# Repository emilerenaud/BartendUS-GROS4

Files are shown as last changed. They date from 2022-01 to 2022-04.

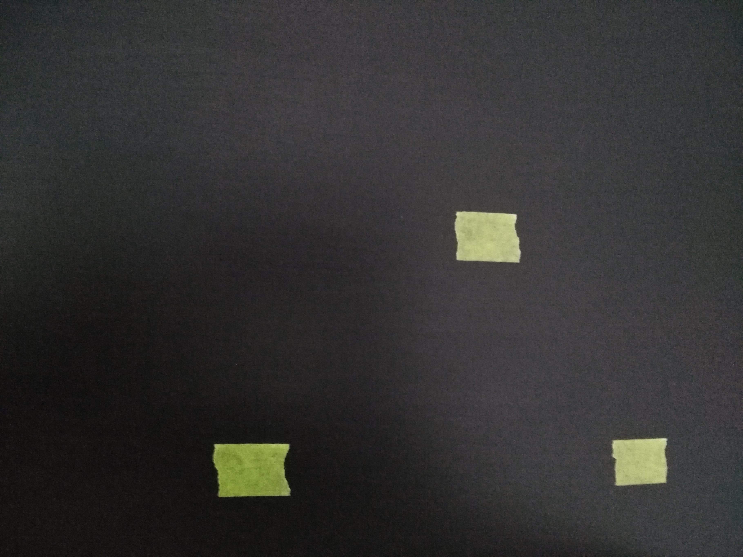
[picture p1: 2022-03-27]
Logiciel/Vision/img_to_seuil.png

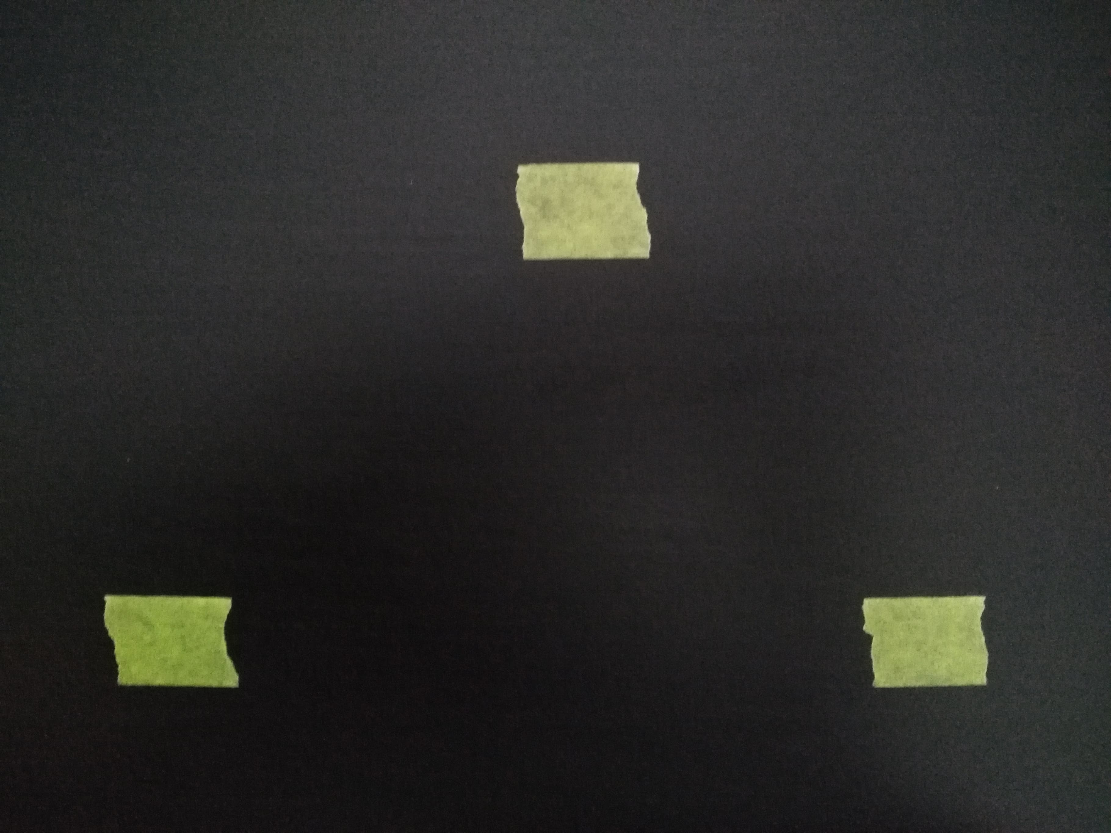
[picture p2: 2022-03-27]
Logiciel/Vision/img_reference_calib_V2.png

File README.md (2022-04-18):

# BartendUS 
## GRO-S4H2022 - Université de Sherbrooke

BartendUS est un projet académique de 4e session du programme de génie robotique de l'Université de Sherbrooke réalisé par 6 étudiants. C'est un projet réalisé dans le cadre du cours _GRO400:_ _Conception agile et ouverte en robotique_.

BartendUS est une plateforme surmontée d'un bras robotisé de type SCARA qui permet de créer des breuvages alcoolisés sur mesure. Le robot est assisté par un algorithme de vision ainsi qu'une interface utilisateur graphique. Également, des supports conçus sur mesure permettent le maintien des bouteilles en place tout en facilitant la distribution des liquides.



## Table des matières
* Présentation de l'équipe
* Vidéo promotionnelle du projet
* Requis matériel
* Installation
* Licence

## Présentation de l'équipe


*De gauche à droite: Simon Chayer, Émile Renaud, Antoine Landry, Hugues Dupuis et Thomas Landry*

IMPORTANT : Sur cette photo, il manque un membre de l'équipe : Frédéric Forest, qui ne pouvait pas être présent lors de la présentation.

## Vidéo promotionnelle du projet
Voici une vidéo réalisée par Antoine Landry mettant en vedette la solution développée tout au long de la session:
https://www.youtube.com/watch?v=95p3Jdjmmvk

## Requis matériel
- Un bras robotisé SCARA et sa plateforme. Les instructions d'assemblage sont disponibles dans [le répertoire « Mécanique »](https://github.com/mimil2014/BartendUS-GROS4/tree/main/M%C3%A9canique).
- Distributeur d'alcool et le support sur mesure. Les plans sont disponibles dans [le répertoire « Mécanique »](https://github.com/mimil2014/BartendUS-GROS4/tree/main/M%C3%A9canique).
- Éléments présentés dans le [BOM](https://github.com/mimil2014/BartendUS-GROS4/blob/main/BOM/liste_pieces.pdf).

## Installation 
### Installation des librairies sur le RaspberryPi:
Assurez-vous que votre Pi est à jour avec les commandes suivantes: 
```
sudo apt update  
sudo apt upgrade  
```
Installer le terminal Terminator (si vous désirez):   
```
sudo apt-get install terminator   
```
Installer Python sur le Pi:   
```
sudo apt install python3-dev   
sudo apt-get install python3-pip 
```
À partir du fichier requirements.txt, installer les librairies avec la commande: 
```
pip3 install -r requirements.txt  
```
Cette commande installera toutes les librairies nécessaires au projet sur votre Pi. Si vous avez de la difficulté à installer OpenCV, vous pouvez suivre les étapes du site suivant:   https://singleboardbytes.com/647/install-opencv-raspberry-pi-4.htm

*Prendre note que la version installée pour ce projet est la version courte détaillée sur le site.

De la façon suggérée sur ce site, les librairies sont installées dans un environnement virtuel. Il faut seulement s'assurer que les autres librairies utilisées     dans le projet sont également dans cet environnement virtuel. 

## Licence
BSD License

Voir [LICENSE](LICENSE)

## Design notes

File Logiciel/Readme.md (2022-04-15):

# Explication des différents sous-dossiers:

## Vision: 
- Calibration de la caméra 
- Détection du seuil

## *pi_controller*:
- Gestion de l'HMI ("*front-end*" et "*back-end*")
- Cinématique inverse
- *Main* du robot
- *State machine*
- Gestion des recettes 
- Gestion des ingéridents et quantités
- Algorithme de détection centre des verres

## *scara_controller*:
- Gestion des moteurs
- Gestion des pompes
- Algorithme de versement
- Algorithme de "*homing*"

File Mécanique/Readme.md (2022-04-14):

# Guide de montage mécanique du robot

Voir le document pdf suivant : [Guide d'assemblage](https://github.com/mimil2014/BartendUS-GROS4/blob/main/M%C3%A9canique/Guide%20d'assemblage%20du%20robot.pdf)

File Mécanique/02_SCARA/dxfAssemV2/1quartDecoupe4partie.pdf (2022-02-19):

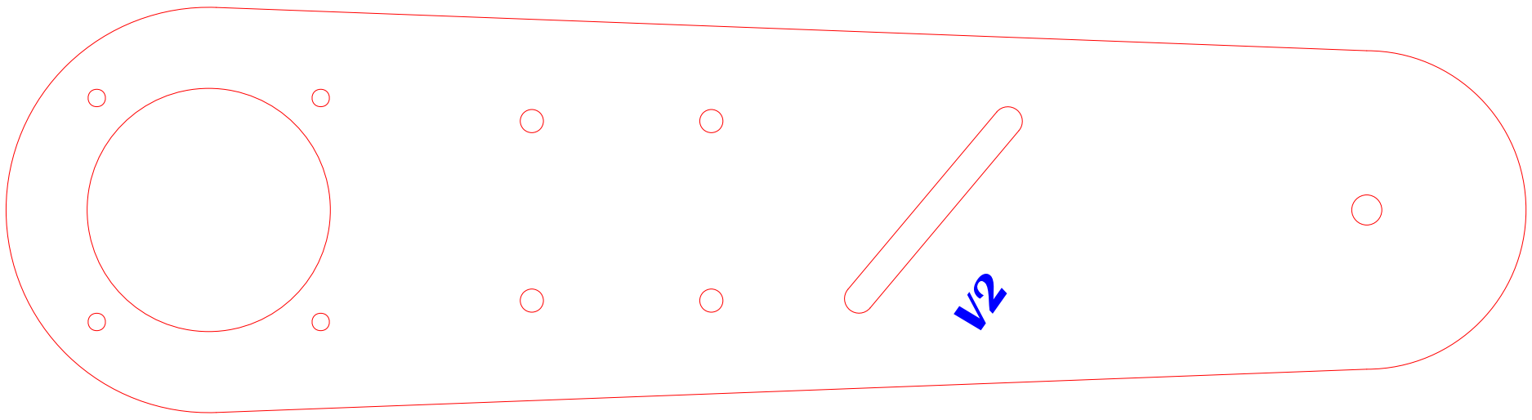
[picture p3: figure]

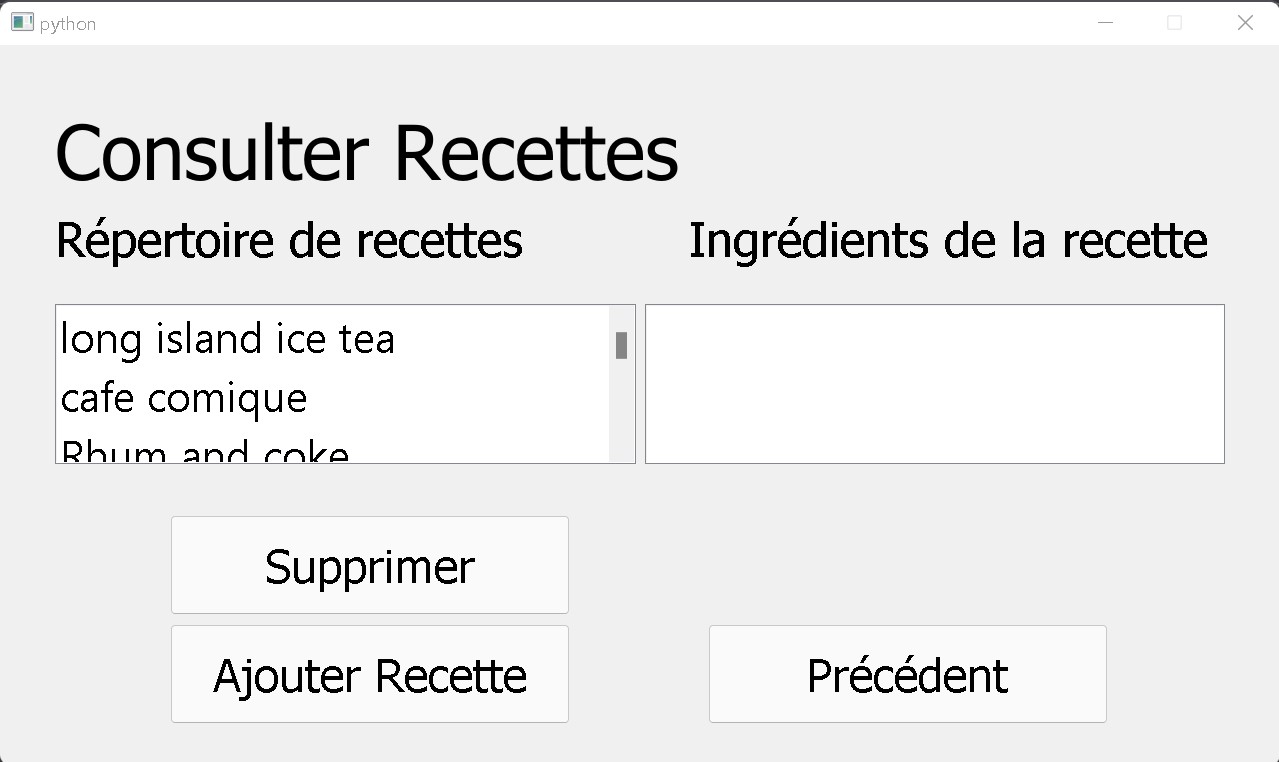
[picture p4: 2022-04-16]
Images/HMI/ecran_consulter_recettes.jpg

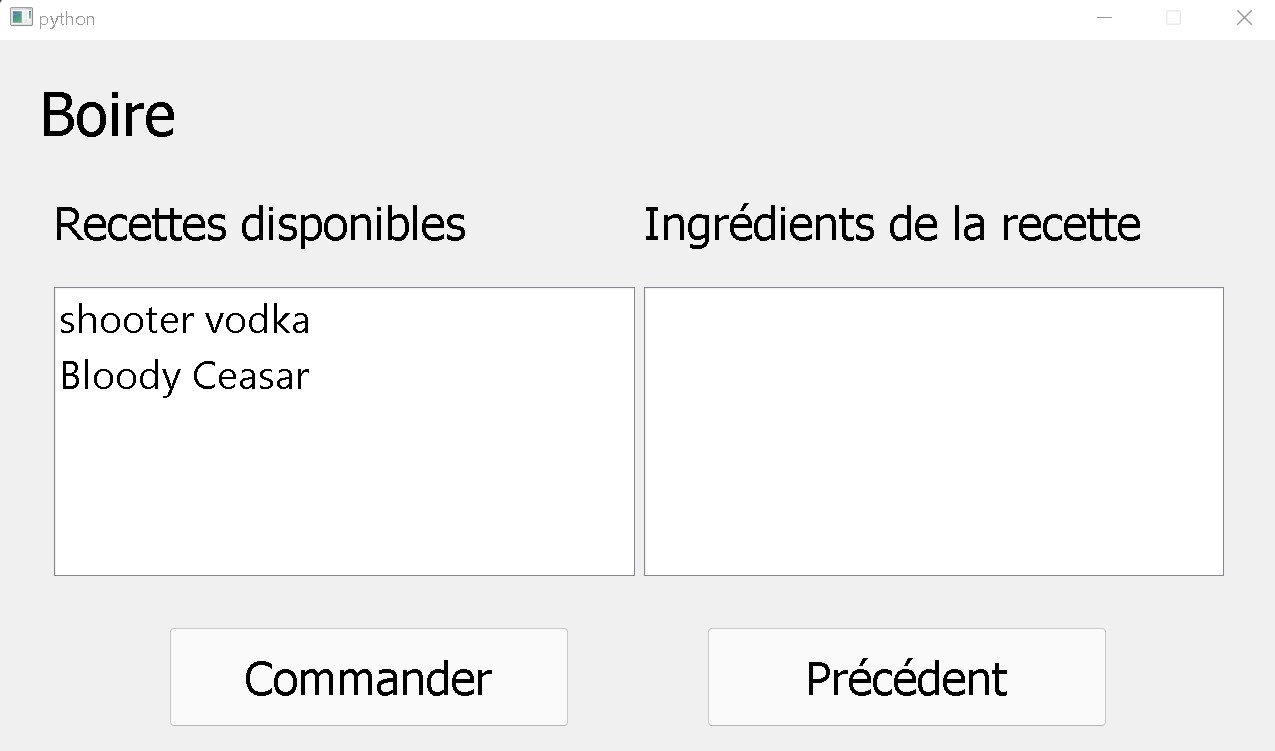
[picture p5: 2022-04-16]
Images/HMI/ecran_boire.jpg

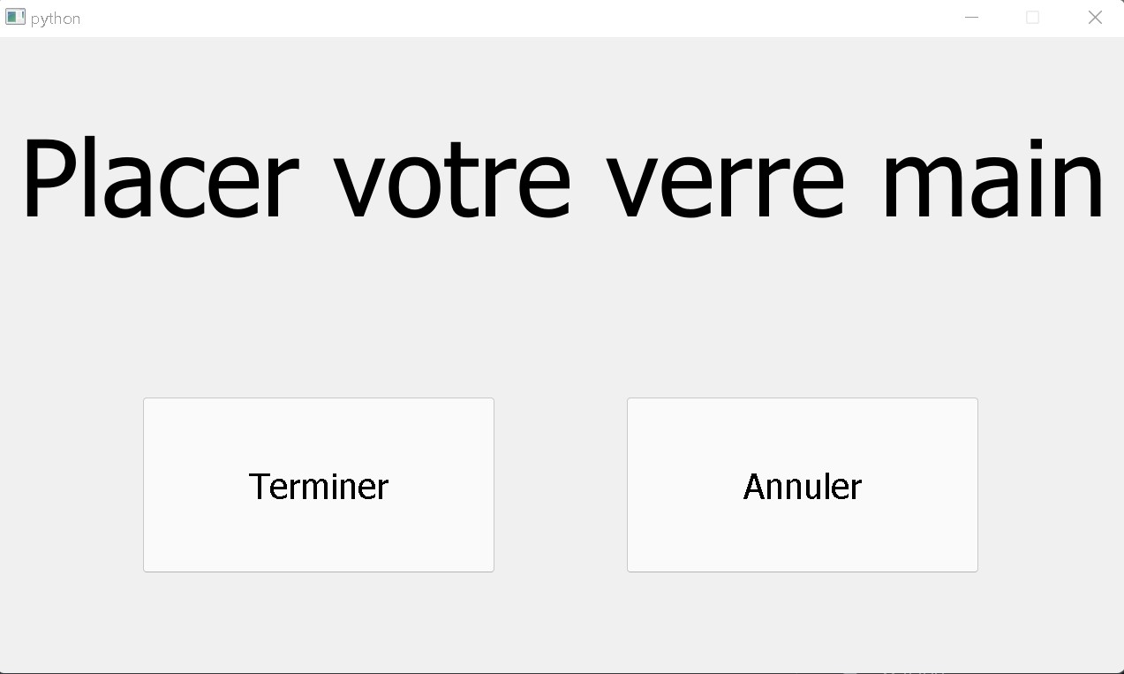
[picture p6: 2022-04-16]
Images/HMI/ecran_commander.jpg

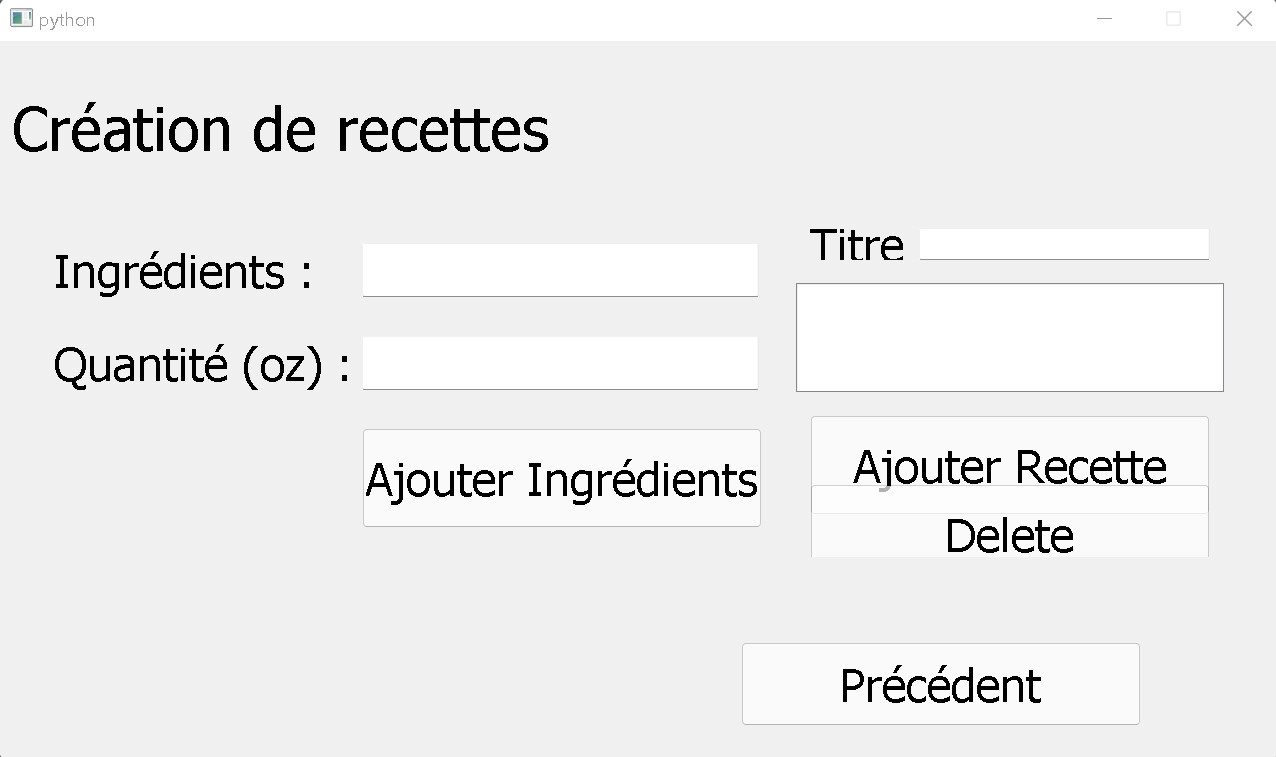
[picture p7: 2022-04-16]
Images/HMI/ecran_ajouter_recette.jpg

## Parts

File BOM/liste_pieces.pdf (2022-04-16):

Domaine | Pièces | Partie du
Robot | Description
Quantité | Coût unitaire | Lieu d’achat | Coût total (CAD)
| (CAD)

Mécanique

Coupleur Nema 17 | Base | | 2 | 2,60 | Amazon | 5,20
Moteur Nema 17 (33
mm) | Base | 33 mm | 3 | 30,03 | Amazon | 90,09
Lead screw | Base | 310 mm T8x8 | 1 | 13,18 | Amazon | 13,18
Tige en acier
inoxydable | Base | 8 x 300 mm | 3 | 21,00 | Amazon | 63,00
Lead Screw Nut | Base | T8 | 2 | 5,00 | Amazon | 10,00
Roulement à billes
pour planche à roulettes | Base | 8 x 22 x 7 mm | 1 | 2,98 | Amazon | 2,98
M4 10 mm + écrou | Base | - | 6 | 0,15 | Amazon | 0,90
M5 10 mm + écrou | Base | - | 13 | 0,15 | Amazon | 1,95
M5 16 mm + écrou | Base | - | 22 | 0,15 | Amazon | 3,30
M5 60 mm + écrou | Base | - | 6 | 0,15 | Amazon | 0,90
Linear Ball Bearings | Chariot | D. axe : 8 mm | 6 | 8,00 | Amazon | 48,00
M3 16 mm + écou | Chariot | - | 4 | 0,15 | Amazon | 0,60
M3 16 mm tête
fraisée + écrou | Chariot | - | 11 | 0,15 | Amazon | 1,65
M3 20 mm + écrou | Chariot | - | 27 | 0,15 | Amazon | 4,05
M5 50 mm + écrou | Chariot | - | 1 | 0,15 | Amazon | 0,15
M8 40 mm + écrou | Chariot | - | 1 | 0,15 | Amazon | 0,15
Thrust ball bearing | Bras | 20 x 40 x 14 mm | 4 | 10,00 | Amazon | 40,00
Micro Servo Moteur
pour RC | Bras | SG90 9 g | 1 | 6,99 | Amazon | 6,99

M3 8 mm tête fraisée
+ écrou | Bras | - | 12 | 0,15 | Amazon | 1,80
M3 10 mm + écrou | Bras | - | 8 | 0,15 | Amazon | 1,20
M4 30 mm + écrou | Bras | - | 4 | 0,15 | Amazon | 0,60

Tableau 1 : Liste de pièces exhaustive du projet

M5 50 mm + écrou Bras

2 | 0,15 | Amazon | 0,30
Shaker | Bras

1 | 35,00 | Amazon | 35,00
M3 10 mm + écrou | Caméra

3 | 0,15 | Amazon | 0,45
M3 16 mm + écrou | Caméra

1 | 0,15 | Amazon | 0,15
M4 16 mm + écrou | Caméra

4 | 0,15 | Amazon | 0,60
Tuyau en aluminium
pour caméra | Caméra | 3,5 pi
1 | 20,00 | Amazon | 20,00
M5 35 mm+ écrou | Distributeur

4 | 0,15 | Amazon | 0,60
Pompe à Membrane 6-12V | Distributeur | R385 DC
6 | 13,9
| 8 | Amazon | 83,88

Tube en silicone

flexible | Distributeur | 6 x 8 mm, Longueur
: 5 m
| | 1 | 16,99 | Amazon | 16,99

Moteur Nema 17 (48
mm) | Chariot/Bras | 48 mm
| | 2 | 13,99 | Amazon | 27,98

Bore Timing Pulley
Idler With Bearing | Chariot/Bras | GT2 20T 5mm Bore
| | 2 | 4,00 | Amazon | 8,00

Bore Timing Belt Idler
Pulley Flange With
Bearing
Chariot/Bras | GT2 20T 5mm Bore | 2 | 3,99 | Amazon | 7,98
Open Belt | Chariot/Bras | GT2 LL
| -2GT -6 (6 mm
| wide)
- 1890 mm
| | 1 | 15,00 | Amazon | 15,00

Inserts M3 pour
impression 3D

Chariot/Bras/
Base | Hauteur : 7mm | 20 | 0,25 | Amazon | 5,00

Passe fil

- | - | 1 | 5,00 | Amazon | 5,00
Contre

-plaqué
merisier russe
- 5 pi x 5 pi
| | 1 | 50,00 | Rona | 50,00

Électrique

Raspberry Pi 4 Starter
Kit
- 4GB RAM
1 | 149,95 | Amazon | 149,95

Arduino Mega 2560
Rev3

1 | 50,64 | Amazon | 50,64

CNC shield

Carte d'extension
Longruner GRBL
CNC Shield V3.0 +
pilote moteur pas à
pas A4988 avec
dissipateur
thermique
1 | 30,99 | Amazon | 30,99

Transistor

- 2N2222
6 | 0,50 | Amazon | 3,00
Diode
- 1N4007

T

6 | 0,30 | Amazon | 1,80

Power Supply

Entrée universelle :
100

-240 V CA ;
sortie : 12 V CC 5 A
1 | 20,99 | Amazon | 20,99
Fiches d'aviation | Distributeur

4 broches 16 mm
GX16

-4 en métal
mâle

-femelle

4 | 3,86 | Amazon | 15,45

Écran tactile
- 7 " de diagonale
1 | 120,00 | Amazon | 120,00
Limit switch | Chariot/Bras/
Base

3 | 0,35 | Amazon | 1,05

Caméra

Caméra

1 | 10,00 | Amazon | 10,00
Électro
-aimant | Bras

1 | 20,00 | Amazon | 20,00
Câble USB

1 | 4,00 | Amazon | 4,00
Total | 1001,49

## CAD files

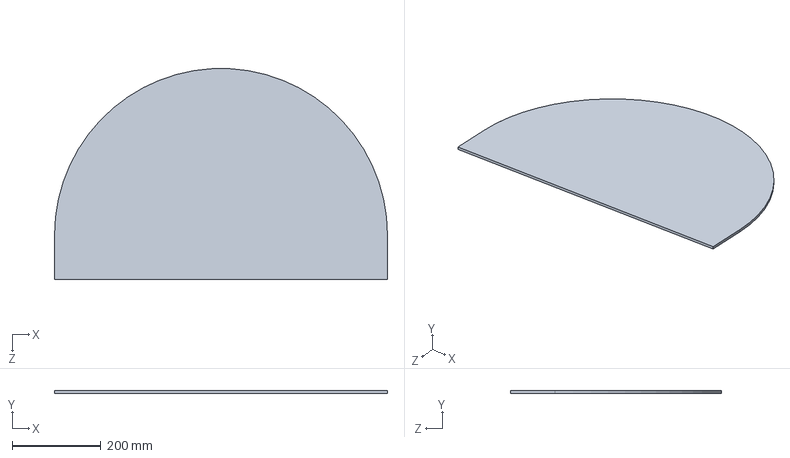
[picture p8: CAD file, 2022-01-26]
Mécanique/00_Assy_BartendUS.SLDASM
750.0 x 6.35 x 474.5 mm

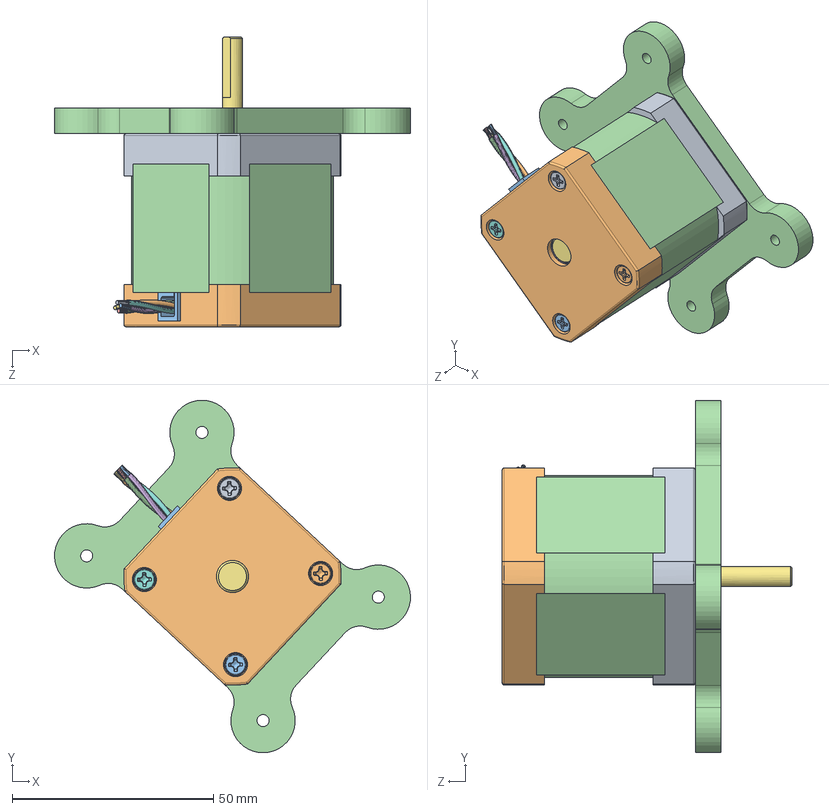
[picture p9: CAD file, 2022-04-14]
Mécanique/02_SCARA/V3/chariotTEST/assemblage_support_stepper_v2_temp.SLDASM
88.5 x 87.6 x 72.0 mm
Frontplate.step
Backplate.step
Connenctor.step
Housing.step
Bearing dummy.step
Bearing dummy 01.step
Core.step
M3x40-Screw.step
M3x40-Screw001.step
M3x40-Screw002.step
M3x40-Screw003.step
Cable-1of4.step
Copper-1of4.step
Cable-2of4.step
Copper-4of4.step
Cable-3of4.step
Copper-3of4.step
Cable-4of4.step
Copper-2of4.step
supportMoteurTop

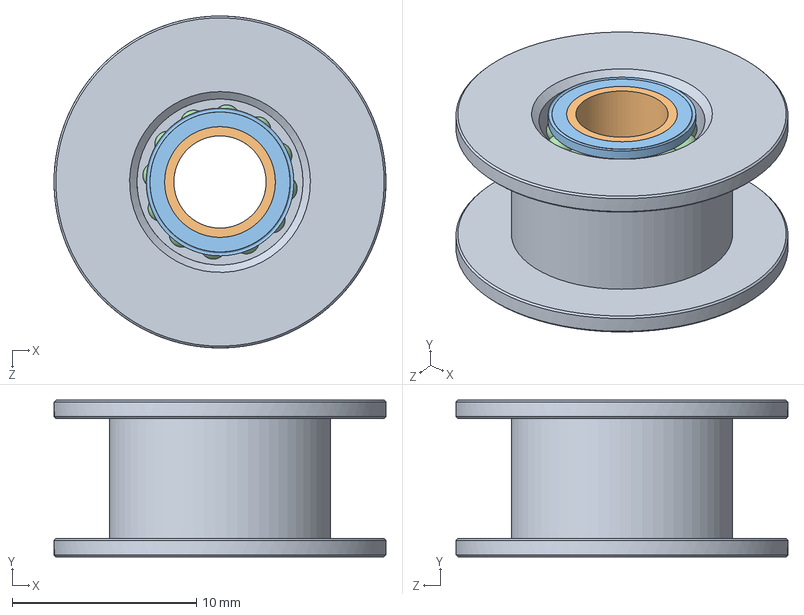
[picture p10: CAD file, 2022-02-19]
Mécanique/99_Library/gt2-pulley-16-20-without-teeth-bore-3-4-5-mm-for-gt2-belt-width-6-10-mm-1.snapshot.84/GT2 Idler Pulley, Configurable.SLDASM
18.0 x 8.50 x 18.0 mm
Body, GT2 Idler Pulley, Configurable
Bearing Inner Ring, GT2 Idler Pulley, Configurable x 2
Bearing Seal, GT2 Idler Pulley, Configurable x 4
Bearing Ball, GT2 Idler Pulley, Configurable x 24

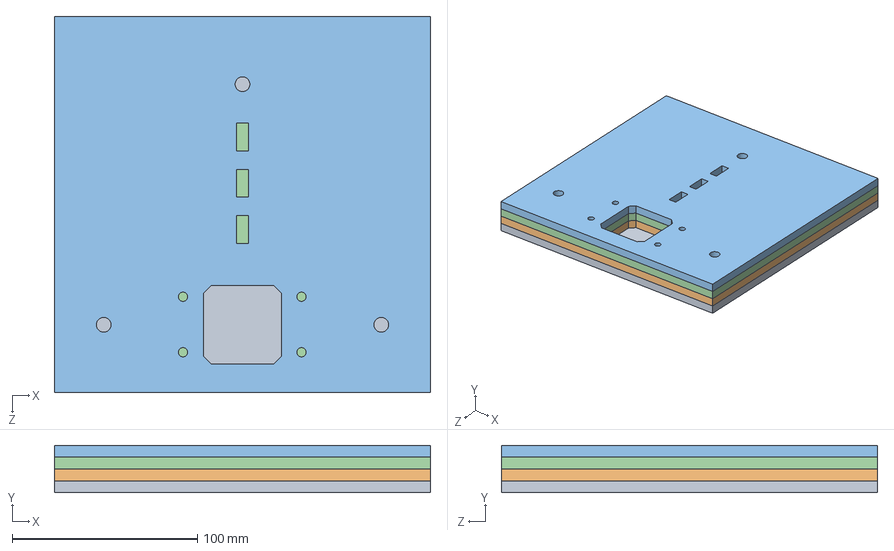
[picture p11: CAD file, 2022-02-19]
Mécanique/02_SCARA/V3/Z-axis/02_01_Assy_base_z_axis_V1.SLDASM
203.2 x 25.4 x 203.2 mm
02_03_plaque_fond_base
02_05_deuxieme_niveau_base
02_06_troixieme_niveau_base
02_012_deuxieme_v2_niveau_base

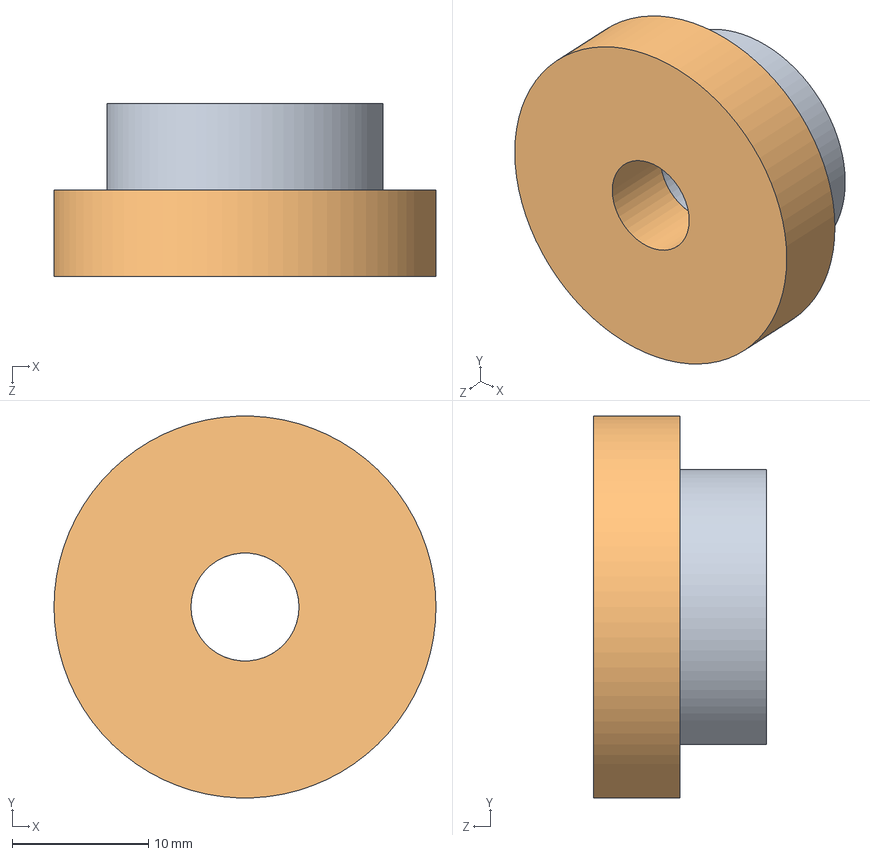
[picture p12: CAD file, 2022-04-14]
Mécanique/03_Supp_distri/V3/assemblage_bouchon.SLDASM
28.0 x 28.0 x 12.7 mm
partie_inf_bouchon_bouteille
partie_supp_bouchon_bouteille

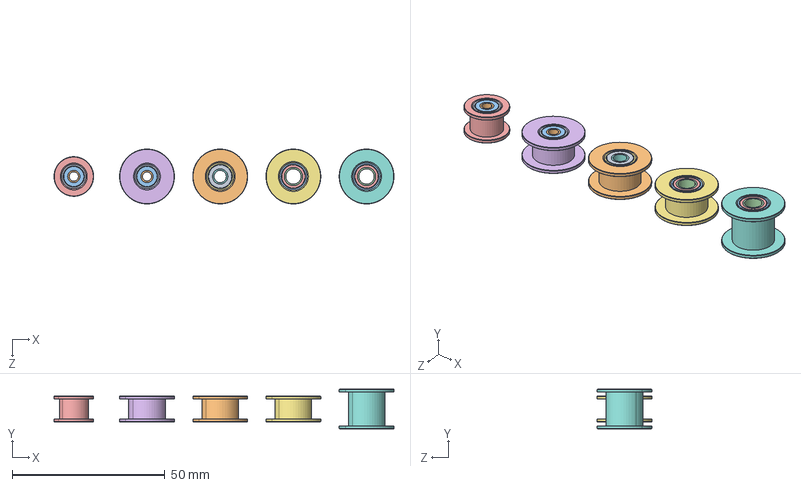
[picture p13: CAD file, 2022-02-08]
Mécanique/99_Library/gt2-pulley-16-20-without-teeth-bore-3-4-5-mm-for-gt2-belt-width-6-10-mm-1.snapshot.84/GT2 Idler Pulley, Configurable, Pulleys Lined Up in Assembly.STEP.SLDASM
111.5 x 13.0 x 18.0 mm
Bearing Outer Ring, GT2 Idler Pulley, Configurable_3 mm Bore.STEP x 4
Bearing Inner Ring, GT2 Idler Pulley, Configurable_3 mm Bore.STEP x 4
Bearing Seal, GT2 Idler Pulley, Configurable_3 mm Bore.STEP x 8
Bearing Ball, GT2 Idler Pulley, Configurable_2 mm.STEP x 40
Body, GT2 Idler Pulley, Configurable_16T W6 B3 Without T.STEP
Body, GT2 Idler Pulley, Configurable_20T W6 B3 Without T.STEP
Bearing Outer Ring, GT2 Idler Pulley, Configurable_4 mm Bore.STEP x 2
Bearing Inner Ring, GT2 Idler Pulley, Configurable_4 mm Bore.STEP x 2
Bearing Seal, GT2 Idler Pulley, Configurable_4 mm Bore.STEP x 4
Body, GT2 Idler Pulley, Configurable_20T W6 B4 Without T.STEP
Bearing Outer Ring, GT2 Idler Pulley, Configurable_5 mm Bore.STEP x 4
Bearing Inner Ring, GT2 Idler Pulley, Configurable_5 mm Bore.STEP x 4
Bearing Seal, GT2 Idler Pulley, Configurable_5 mm Bore.STEP x 8
Bearing Ball, GT2 Idler Pulley, Configurable_1.4 mm.STEP x 48
Body, GT2 Idler Pulley, Configurable_20T W6 B5 Without T.STEP
Body, GT2 Idler Pulley, Configurable_20T W10 B5 Without T.STEP

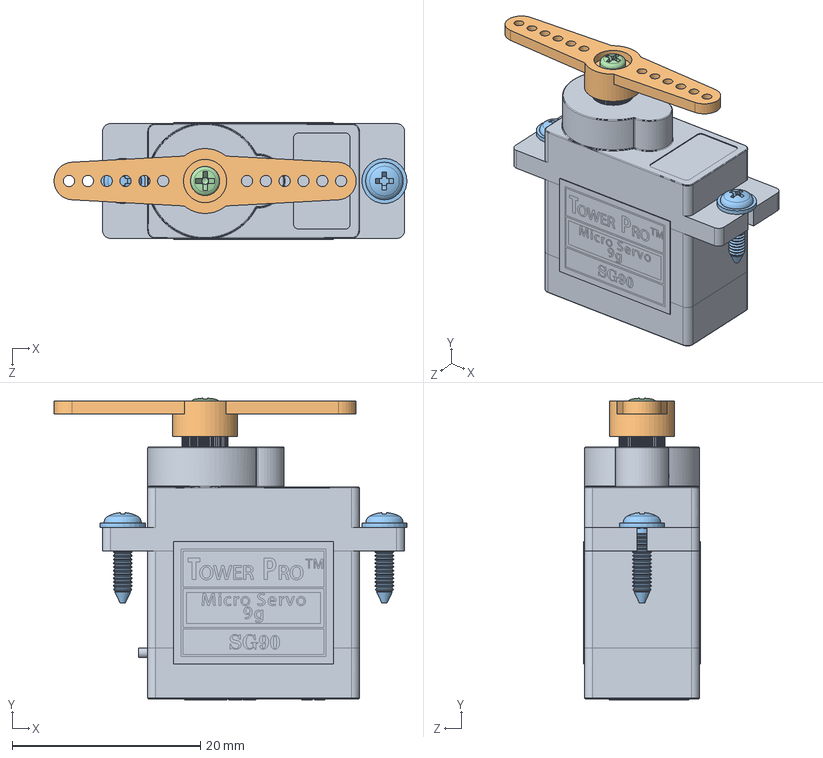
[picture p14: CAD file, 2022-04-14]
Mécanique/99_Library/SG90 - Micro Servo 9g - Tower Pro.SLDASM
37.5 x 32.0 x 12.4 mm
SG90 - Micro Servo 9g - Tower Pro.1
SG90 - Micro Servo 9g - Tower Pro.3
SG90 - Micro Servo 9g - Tower Pro.5 x 2
SG90 - Micro Servo 9g - Tower Pro.6

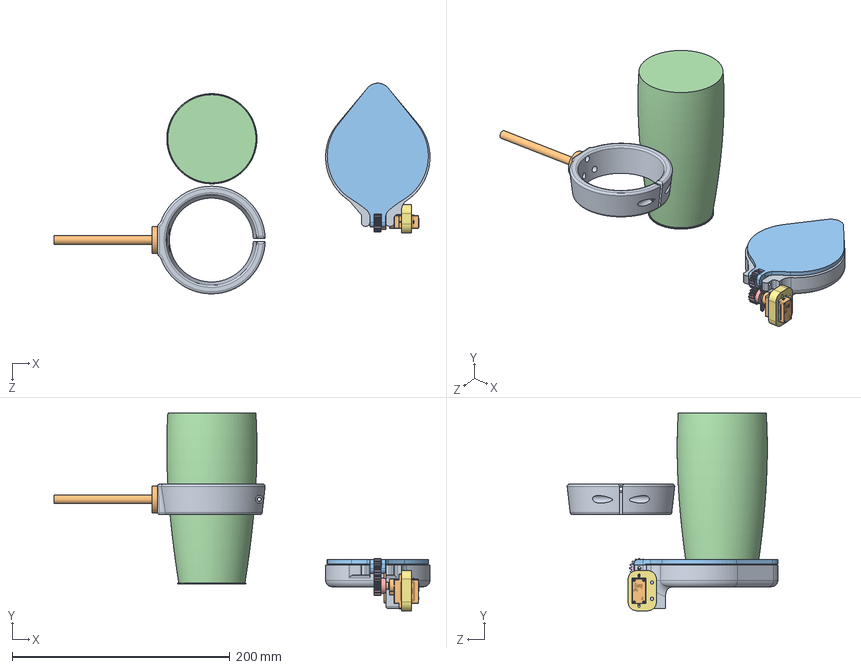
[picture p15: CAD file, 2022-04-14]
Mécanique/Shaker/Assem2.SLDASM
345.7 x 181.7 x 193.8 mm
topShaker
SG90 - Micro Servo 9g - Tower Pro
coverV2
shaker
ServoGear
coverGear
suuportServo
gasketproto2
supportShakerV3
shaft

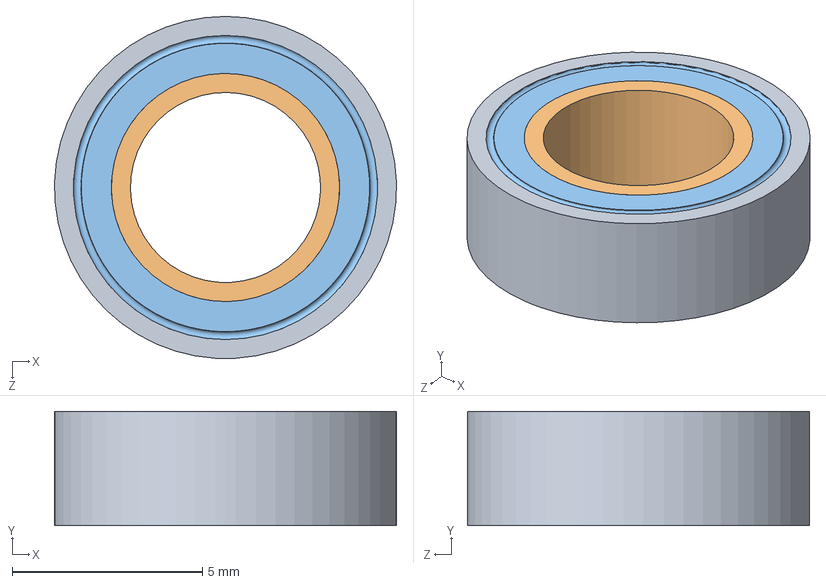
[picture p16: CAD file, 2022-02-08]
Mécanique/99_Library/gt2-pulley-16-20-without-teeth-bore-3-4-5-mm-for-gt2-belt-width-6-10-mm-1.snapshot.84/Bearing Subassy, GT2 Idler Pulley, Configurable.SLDASM
9.00 x 3.00 x 9.00 mm
Bearing Outer Ring, GT2 Idler Pulley, Configurable
Bearing Inner Ring, GT2 Idler Pulley, Configurable
Bearing Seal, GT2 Idler Pulley, Configurable x 2
Bearing Ball, GT2 Idler Pulley, Configurable x 12

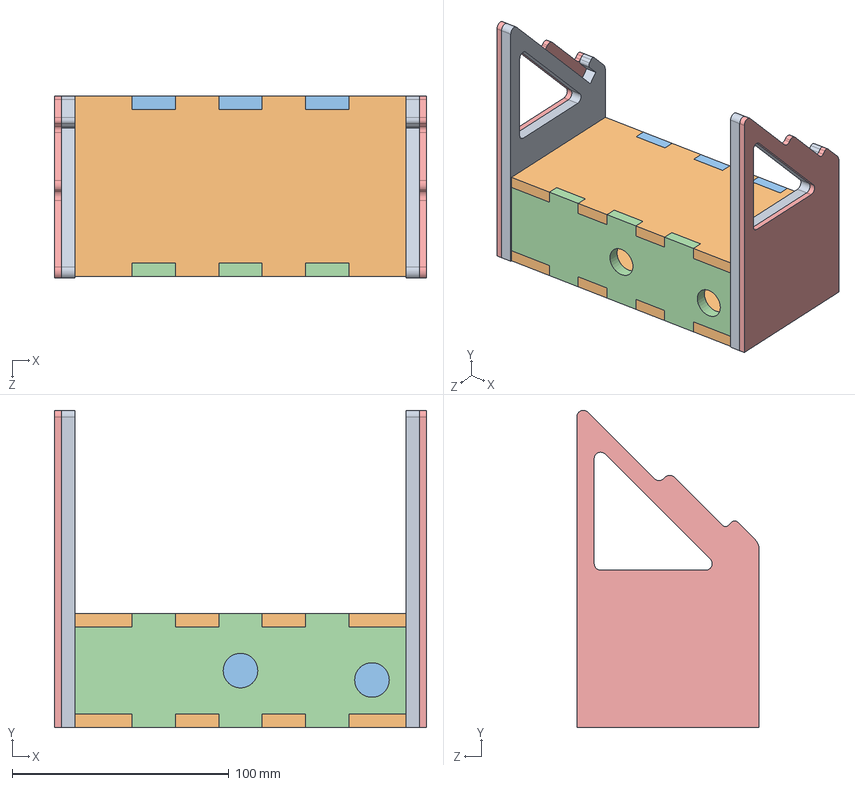
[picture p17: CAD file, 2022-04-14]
Mécanique/01_Base/V1/Support écran/ass_support_ecran.SLDASM
171.7 x 146.5 x 84.1 mm
montant_exterieur_support_ecran x 2
plancher_support_ecran x 2
face_support_ecran
arriere_support_ecran
montant_exterieur_support_ecran_1_8 x 2

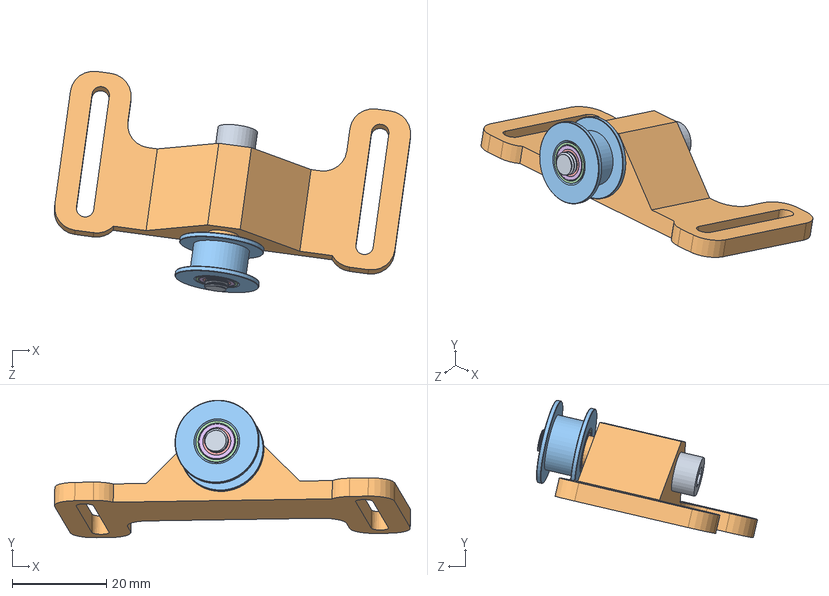
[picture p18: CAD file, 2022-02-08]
Mécanique/99_Library/gt2-pulley-16-20-without-teeth-bore-3-4-5-mm-for-gt2-belt-width-6-10-mm-1.snapshot.84/AssemSupportPoulie.SLDASM
75.7 x 29.3 x 47.1 mm
M5x30.stp
supportPoulieV2
Body, GT2 Idler Pulley, Configurable
Bearing Outer Ring, GT2 Idler Pulley, Configurable x 2
Bearing Inner Ring, GT2 Idler Pulley, Configurable x 2
Bearing Seal, GT2 Idler Pulley, Configurable x 4
Bearing Ball, GT2 Idler Pulley, Configurable x 24

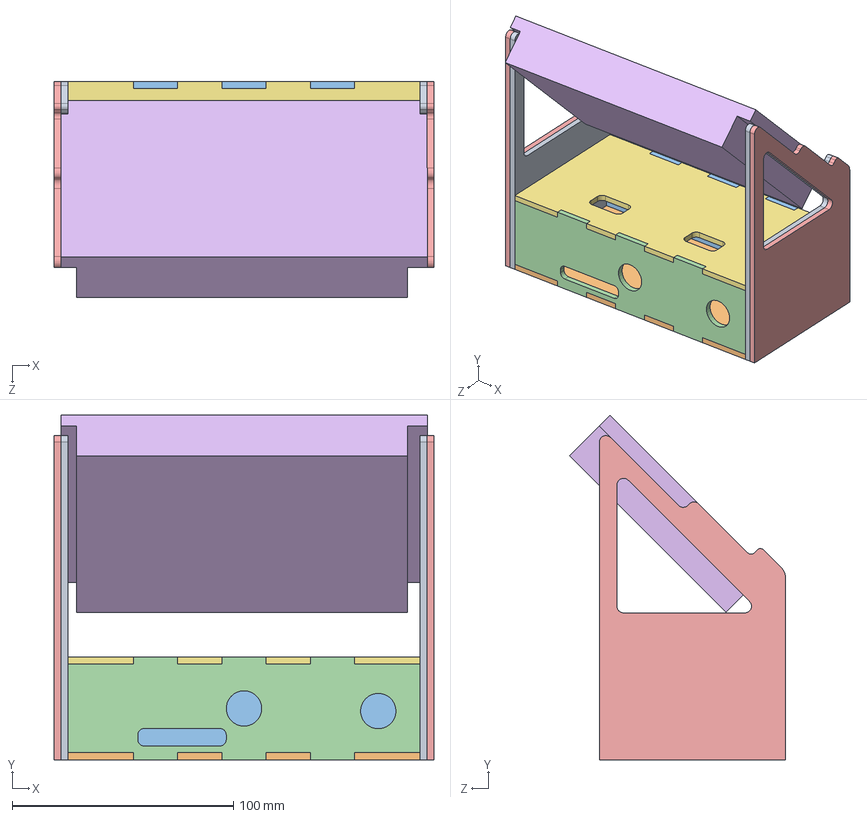
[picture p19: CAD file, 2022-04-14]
Mécanique/01_Base/V1/Support écran/1_8_po/support_ecran_1_8_po.SLDASM
171.7 x 155.7 x 97.6 mm
montant_exterieur_support_ecran_1_8_int x 2
plancher_support_ecran_1_8
face_support_ecran_1_8
arriere_support_ecran_1_8
montant_exterieur_support_ecran_1_8 x 2
ecran_7po
plancher_support_ecran_1_8_trous

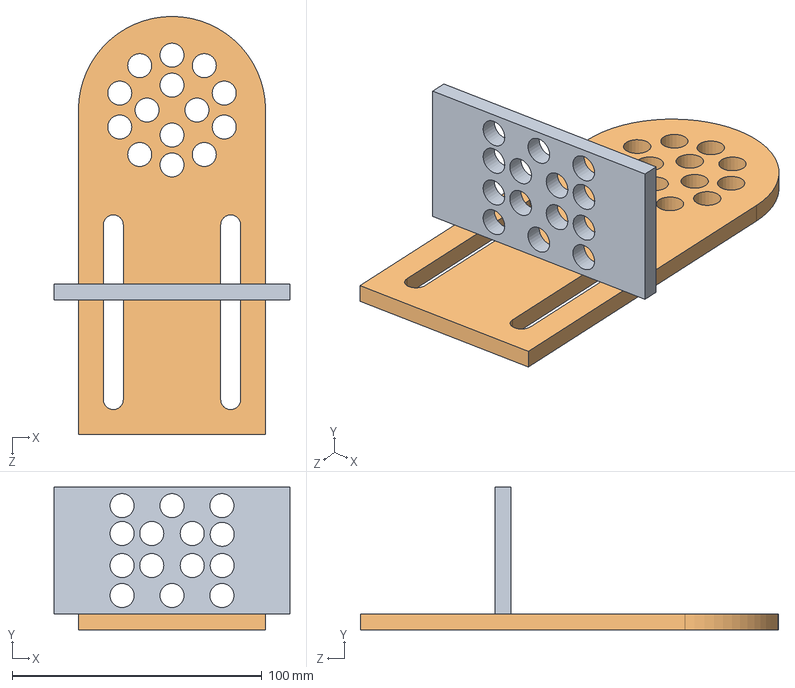
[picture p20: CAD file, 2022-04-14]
Mécanique/03_Supp_distri/V3/Assem.SLDASM
94.5 x 57.2 x 167.5 mm
protoDistributeurTOP
protoDistributeur

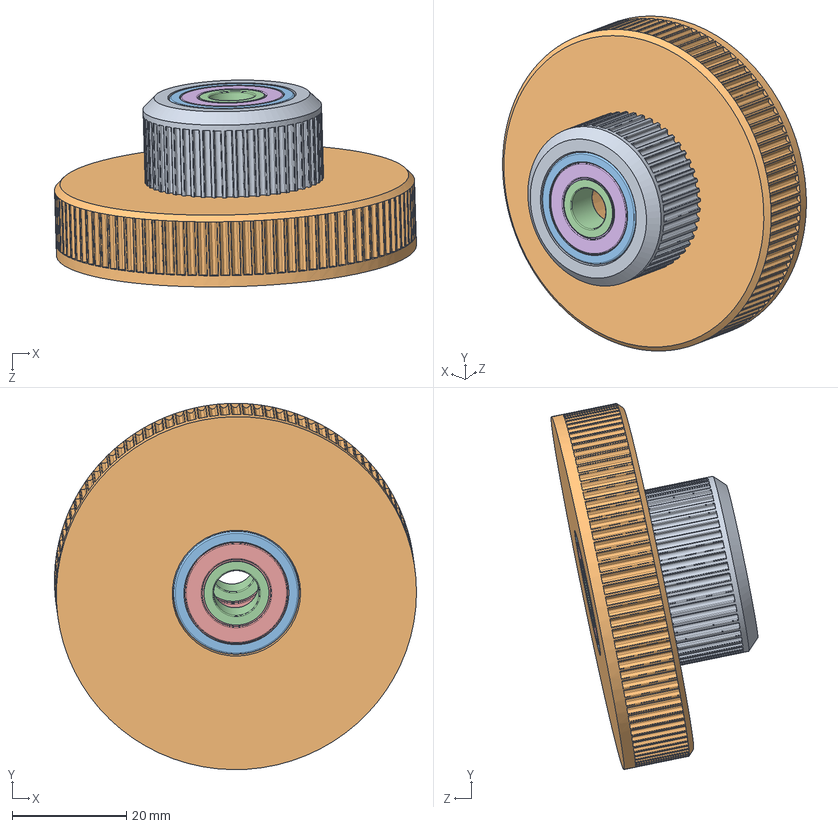
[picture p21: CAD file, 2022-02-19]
Mécanique/02_SCARA/V3/chariotTEST/pulleyRatio2.SLDASM
63.4 x 64.2 x 36.3 mm
50teethPulley
100teethPulley
Ball 001.step x 2
Ball 002.step x 2
Ball 003.step x 2
Ball 004.step x 2
Ball 005.step x 2
Ball 006.step x 2
Ball 007.step x 2
Cage 001.step x 2
Cage 002.step x 2
Rivet 001.step x 2
Rivet 002.step x 2
Rivet 003.step x 2
Rivet 004.step x 2
Rivet 005.step x 2
Rivet 006.step x 2
Rivet 007.step x 2
Outer Ring001.step x 2
Inner Ring001.step x 2
Seal 001.step x 2
Seal 002.step x 2

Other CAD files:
Mécanique/01_Base/V1/1_00_Assy_Base_V1.SLDASM
Mécanique/99_Library/gt2-pulley-16-20-without-teeth-bore-3-4-5-mm-for-gt2-belt-width-6-10-mm-1.snapshot.84/GT2 Idler Pulley, Configurable, Pulleys Lined Up in Assembly.STEP
Mécanique/02_SCARA/V3/bras_AB/03_01_AssemMidArm.SLDASM
Mécanique/01_Base/V1/Support écran/1_8_po/montant_exterieur_support_ecran_1_8.SLDPRT
Mécanique/01_Base/V1/1_01_Base_V1.SLDPRT
Mécanique/01_Base/V1/Support écran/1_8_po/DXF/arriere_support_ecran_1_8.DXF
Mécanique/01_Base/V1/Support écran/1_8_po/DXF/face_support_ecran_1_8.DXF
Mécanique/01_Base/V1/Support écran/1_8_po/DXF/montant_exterieur_support_ecran_1_8.DXF
Mécanique/01_Base/V1/Support écran/1_8_po/DXF/montant_exterieur_support_ecran_1_8_int.DXF
Mécanique/01_Base/V1/Support écran/1_8_po/DXF/plancher_support_ecran_1_8.DXF
Mécanique/01_Base/V1/Support écran/1_8_po/DXF/plancher_support_ecran_1_8_trous.DXF
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

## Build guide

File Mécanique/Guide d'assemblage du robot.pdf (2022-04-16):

UNIVERSITÉ DE SHERBROOKE
Faculté de génie
Département de génie robotique

## GUIDE D’ASSEMBLAGE DU ROBOT

## Projet : BartendUS

Par :
Frédéric Forest
Hugues Dupuis
Antoine Landry
Thomas Landry
Émile Renaud

### Sherbrooke – Avril 2022

i

## TABLE DES MATIÈRES

1. | Outils nécessaires à l’assemblage | 2
2. | Assemblage axe Z | 2
3. | Assemblage chariot | 11
4. | Assemblage sections A et B du bras | 14
5. | Assemblage du préhenseur et du « Shaker » | 18
6. | Assemblage distributeur | 20
6.1 | Station de remplissage | 20
6.2 | Support à pompes | 25
6.3 | Présentoir à bouteilles | 26
7. | Support de la caméra | 29
8. | Support à écran | 30
9. | Assemblage plateforme | 32

## 1.OUTILS NÉCESSAIRES À L’ASSEMBLAGE

- Clés hexagonales M2 à M6
- Fusil à colle chaude (avec bâtons de colle)
- Imprimante 3D (avec filament (PLA pour ce projet)
- Découpeuse laser
- Pince à dénuder
- Fer à souder
- Colle à bois (avec des serres pour maintenir les pièces en place lors du collage)
- Colle contact pour les plus petites pièces
- Ensemble de douilles métriques et impériales

À moins d’une indication contraire, toutes les pièces sont fabriquées en contreplaqué ¼ po

d’épaisseur découpées au laser.

## 2.ASSEMBLAGE AXE Z

L’assemblage de l’axe Z est assez simple. Une fois toutes les pièces découpées et imprimées, voici

les différentes étapes :

1. Coller les deux pièces supérieures avec de la colle à bois (de cette façon, les pièces auront

le temps de sécher en montant le reste de l’axe Z) :

En utilisant des pinces pour maintenir les pièces ensembles :

2. Superposer les deux morceaux de la base ayant des encoches permettant le passage des

fils en plus des formes des moteurs en s’assurant que celui avec des trous de la forme

d’un écrou aux 4 coins soit sur le dessus!

3. Mettre les deux moteurs en position tout en plaçant un écrou à chaque coin. Mettre les

coupleurs flexibles sur les moteurs

4. Ajouter la plaque comprenant la forme des moteurs et qui contient la plupart des trous

de forme d’écrous par-dessus les deux dernières plaques. (Cette opération peut être

difficile si l’alignement des moteurs n’est pas optimal) Ajouter également les écrous dans

les trous permettant de les recevoir sur cet étage

5. Ajouter la plaque supérieure sur la dernière plaque ajoutée. Celle-ci contient 6 trous en

forme d’écrou qui permettront de serrer la base avec la plateforme

6. Ajouter 4 vis à chaque coin pour solidifier l’assemblage jusqu’à présent (il manque les

moteurs sur cette photo, mais cela revient au même). Ajouter également les 6 écrous

dans les trous de forme d’écrou de cet étage

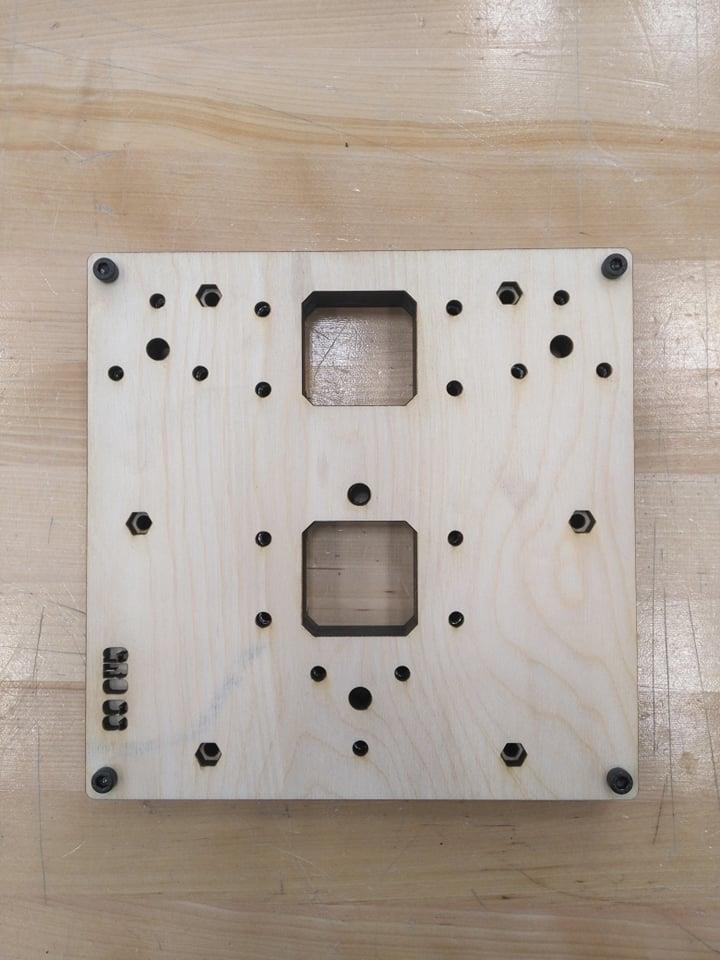
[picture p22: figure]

7. Installer les deux supports de moteurs sur cette dernière plaque

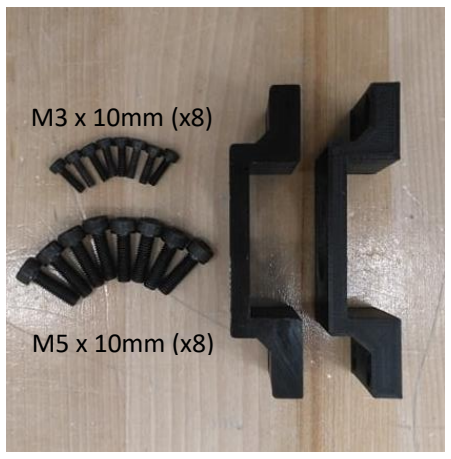
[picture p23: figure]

8. Installer l’assemblage jusqu’à présent sur la plateforme et utiliser 6 vis M5 X 35mm pour

fixer les deux ensembles en s’assurant de mettre le gros écrou central entre les deux

plaques :

9. Installer les 3 supports de tige linéaires ainsi que les 3 tiges en s’assurant de les pousser

jusqu’au fond!

10. Ajouter la tige filetée permettant de consolider l’assemblage avec un écrou et une

rondelle

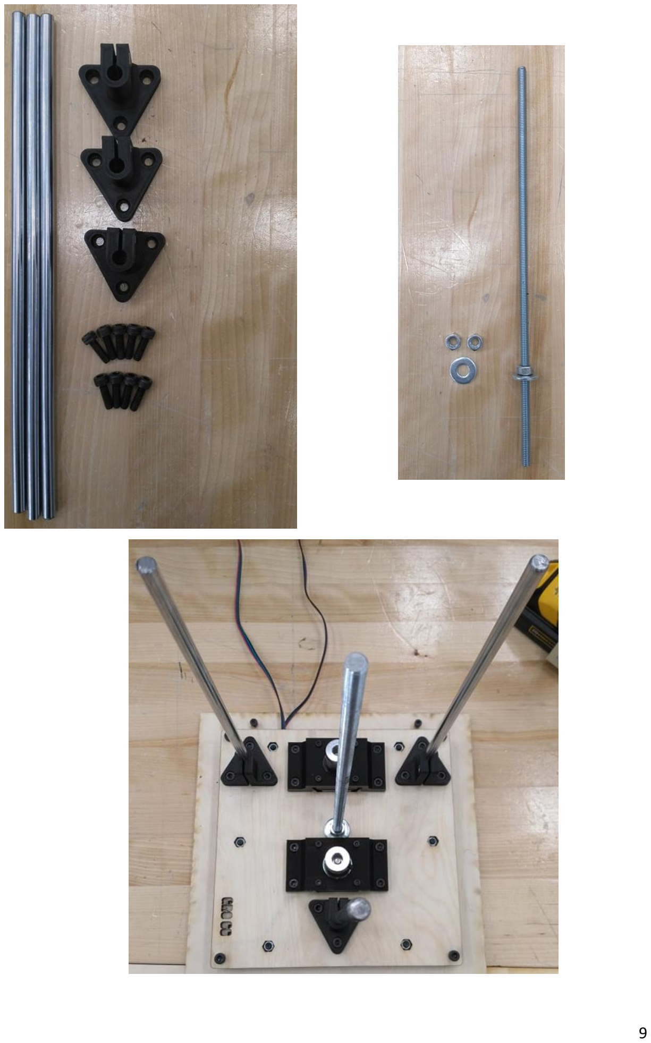
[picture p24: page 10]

11. Fixer les deux tiges filetées T8 sur les coupleurs des deux moteurs

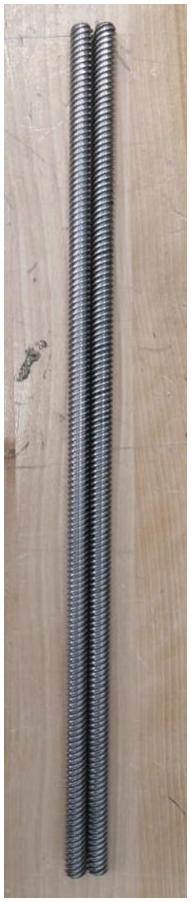
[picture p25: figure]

12. Installer les petits supports de tige lisses sur la plateforme du haut qui a été collé à l’étape

1

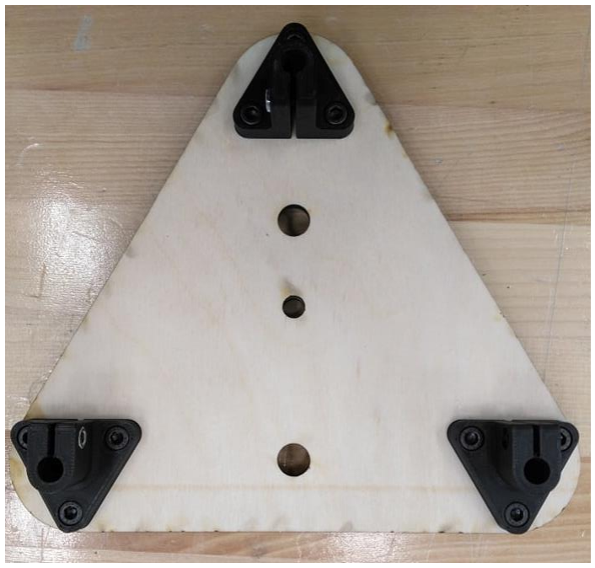
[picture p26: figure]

Rendu ici, il faut maintenant assembler les bras et le chariot. Le haut de l’axe Z sera ajouté lorsque

le chariot sera installé sur les tiges linéaires (dernière étape d’assemblage du robot).

## 3.ASSEMBLAGE CHARIOT

1. Il faut d’abord coller les pièces de 1/8 et de ¾ de pouce ensemble en mettant les pièces

de 1/8 vers l’intérieur du montage. Difficile de se tromper avec la « queue » que les deux

pièces supérieures ont.

2. Insérer les roulements à billes linéaires dans les 4 pièces imprimée prévues à cet effet :

3. Sur la partie inférieure du chariot (celle sans la « queue »), installer les supports et

colonnes, les tensionneurs de poulie et les deux pièces permettant de guider les tiges

filetées (« lead screws ») T8.

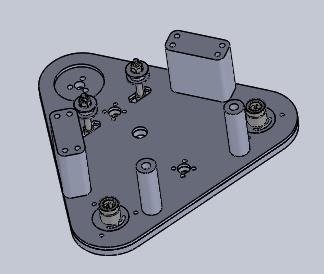
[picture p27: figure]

4. Glisser cette partie dans les trois rails de l’axe Z jusqu’en bas en s’assurant de mettre la

partie ouverte vers le haut

5. Mettre les roulements à billes sur la partie inférieure du chariot
6. Fixer la plaque de support du moteur pas-à-pas à l’aide de 4 vis M3 :
7. Fixer cet assemblage à la partie supérieure du chariot

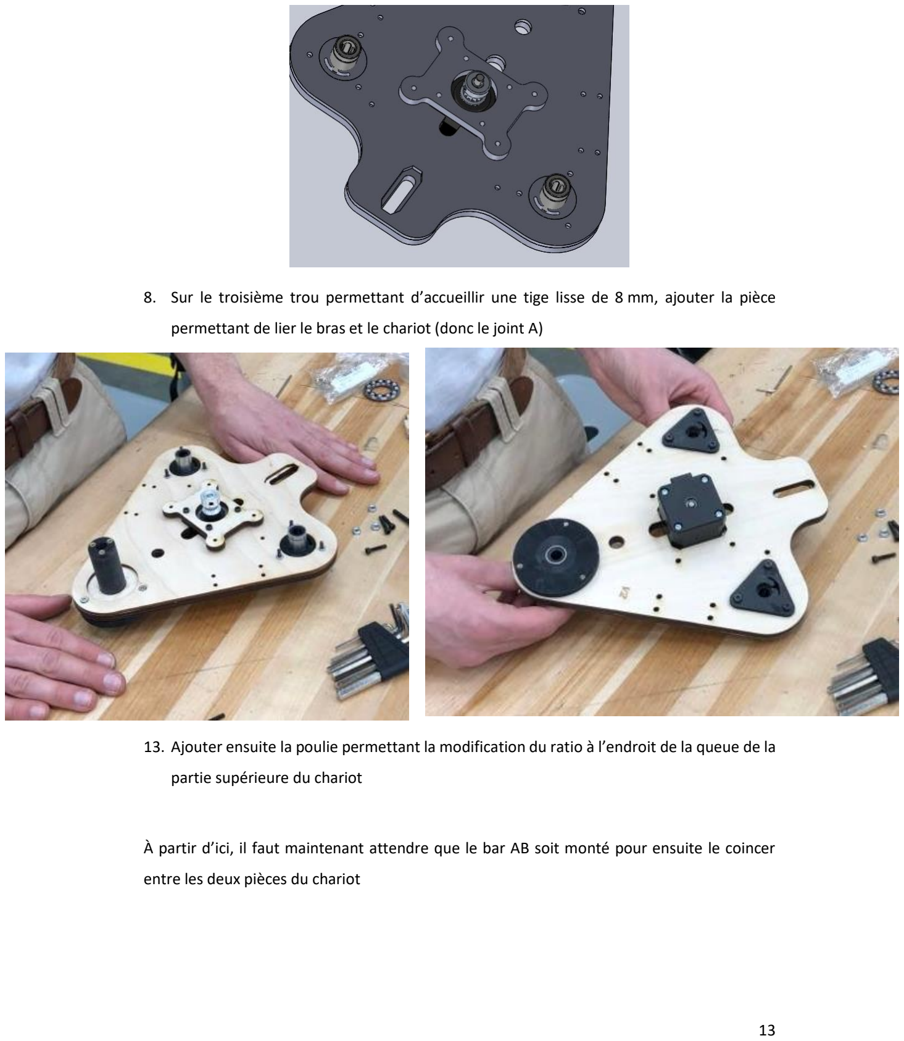
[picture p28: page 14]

8. Sur le troisième trou permettant d’accueillir une tige lisse de 8 mm, ajouter la pièce

permettant de lier le bras et le chariot (donc le joint A)

13. Ajouter ensuite la poulie permettant la modification du ratio à l’endroit de la queue de la

partie supérieure du chariot

À partir d’ici, il faut maintenant attendre que le bar AB soit monté pour ensuite le coincer

entre les deux pièces du chariot

## 4.ASSEMBLAGE SECTIONS A ET B DU BRAS

Le bras se sépare en deux parties :

La section du joint A et la section du joint B.

Il faut commencer par l’assemblage de la section B, soit celle qui est la plus éloignée du robot.

1. Fixer le moteur à la plaque prévue à cet effet
2. Assembler le reste du bras en commençant par le bas comme présenté sur la photo

suivante :

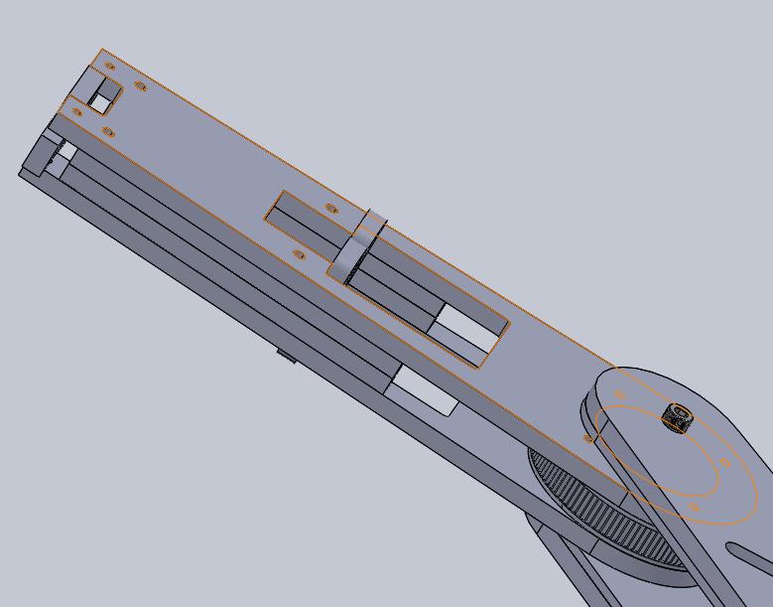
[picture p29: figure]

Porter une attention particulière à intégrer la courroie entre la partie supérieure et la

partie inférieure avant de serrer les vis et de prendre la poulie en sandwich.

Pour les vis servant à serrer la poulie, il faut d’abord fraiser les trous dans les pièces de

bois pour que les têtes de vis ne dépassent pas :

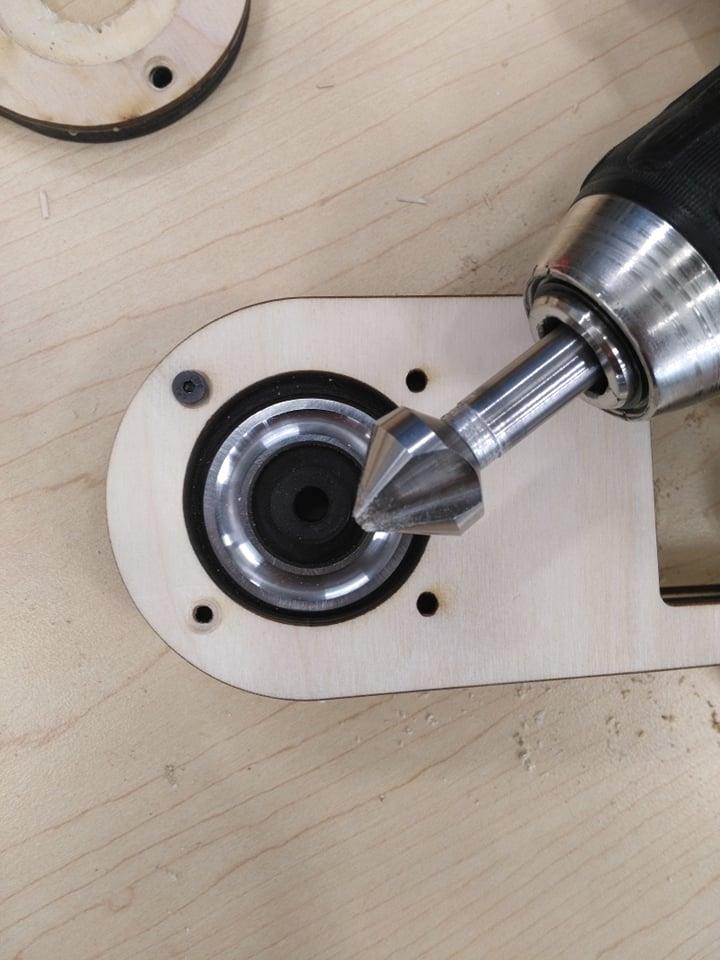
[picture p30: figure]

3. L’assemblage final devrait ressembler à cela :

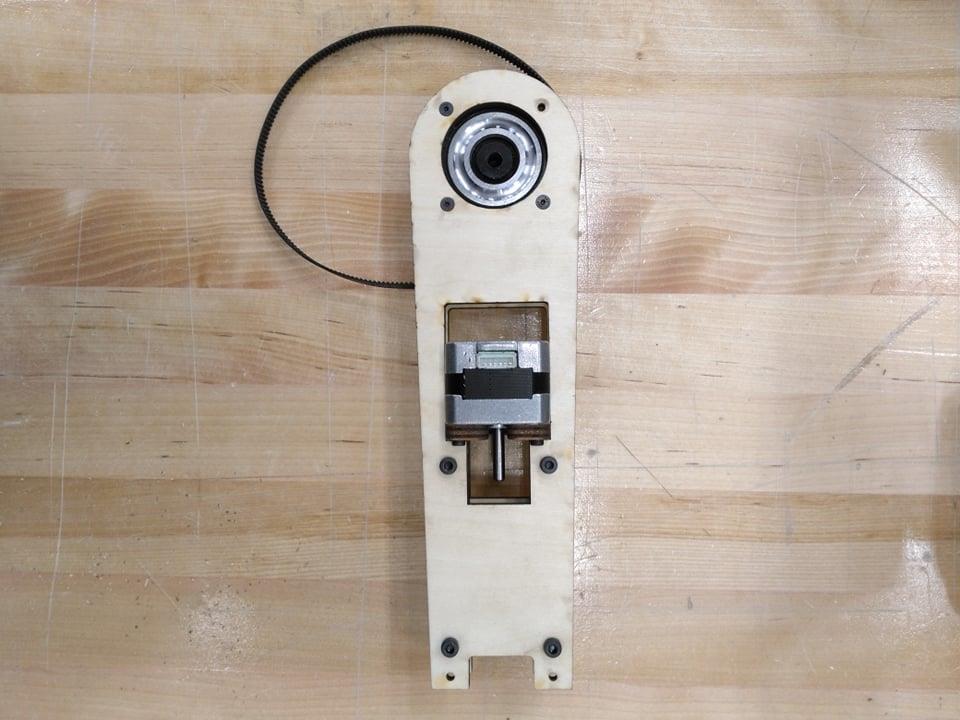
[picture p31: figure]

Maintenant que le joint B est réalisé, il est temps de passer au joint A.

4. Commencer par insérer le bas des roulements à billes dans les pièces d’acrylique. Un

marteau est nécessaire pour faire un beau travail :

5. Installer le moteur sur son support :
6. Installer par la suite la grosse poulie sur la partie inférieure de cette pièce

7. Mettre les roulements à billes sur la section B et l’installer sur la partie inférieure de la

section A

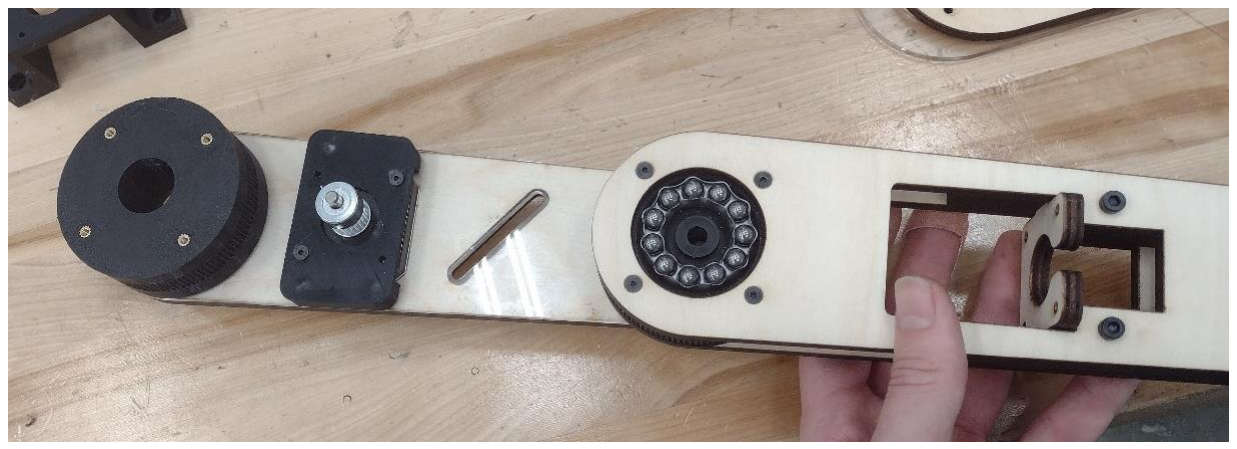
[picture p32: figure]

8. Installer ensuite le tensionneur et la partie supérieure de la section B
9. Visser le joint entre la section A et la B avec une vis et un écrou en nylon pour éviter le

desserrage. Ne pas trop serrer, il faut que le mouvement soit encore fluide.

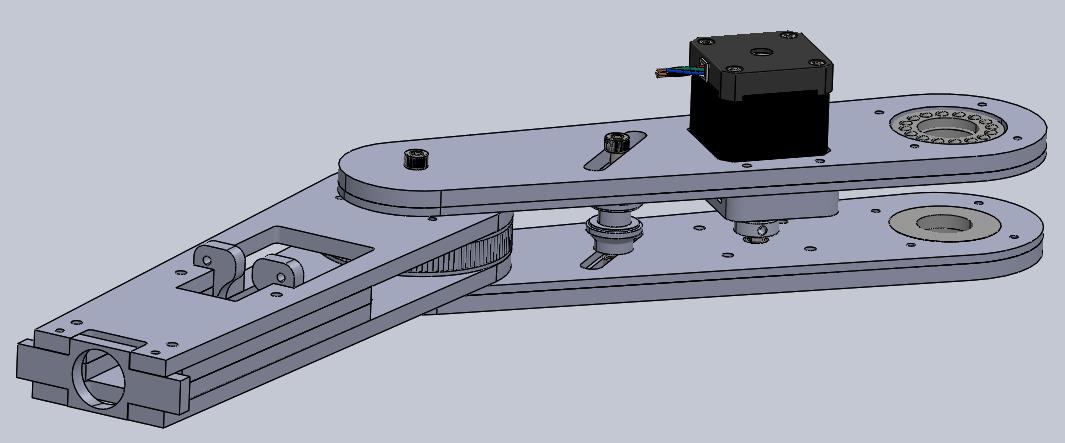
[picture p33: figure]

Le bras est maintenant terminé d’assemblée.

Maintenant, il faut glisser le bras dans le chariot et ensuite visser la partie supérieure du chariot

pour prendre le bras en sandwich.

Il reste maintenant à installer la partie supérieure de l’axe Z. Il suffit de l’installer par-dessus des

3 tiges linéaires et serrer les vis des pièces triangulaires pour stabiliser le tout. Il faut également

boulonner la tige en plein milieu permettant d’encore plus solidifier la structure.

Passer ensuite la courroie passant du moteur sur le chariot vers la section A du bras :

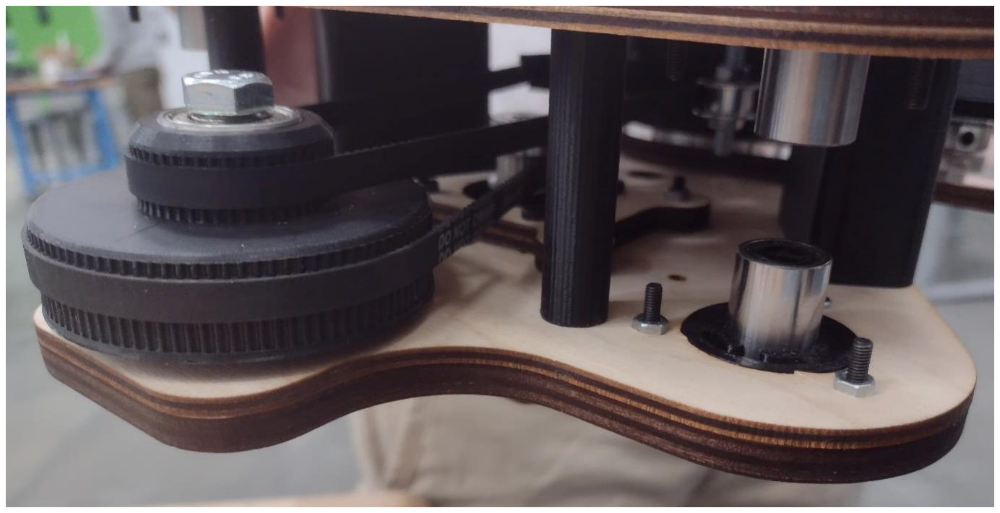
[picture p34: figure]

## 5.ASSEMBLAGE DU PRÉHENSEUR ET DU « SHAKER »

L’assemblage du préhenseur est assez simple. Il faut d’abord insérer des écrous en laiton à chaud

dans la pièce imprimée entre le moteur et le bout du bras. Par la suite, il suffit d’y fixer le support

à « shaker » également imprimé en 3D à l’aide de 3 vis.

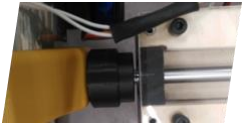
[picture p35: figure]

Pour assurer un meilleur maintien du récipient faisant office de « shaker », il faut y installer de

petites bandes de caoutchouc. Ces derniers peuvent être collés en utilisant de la colle contact ou

encore, il existe de bande de caoutchouc ayant un des deux côtés autocollants.

Pour sécuriser encore plus l’assemblage récipient préhenseur, insérer un boulon et un écrou dans

la fente prévue à cet effet et serrer jusqu’à ce que les deux pièces soient solidaires. Placer la pièce

supportant le servomoteur sur le dessus du « shaker » et insérer l’engrenage au bout du moteur.

Fixer maintenant de couvercle avec une petite pièce en métal.

## 6.ASSEMBLAGE DISTRIBUTEUR

La station de remplissage et le présentoir à bouteilles sont fusionnés ensemble dans un

assemblage compact. Celui-ci est fait majoritairement en contreplaqué découpé au laser ¼ po et aussi de quelques pièces de PLA imprimées en 3D pour les parties en contact avec l’eau. À l’arrière

du présentoir se trouve aussi un tiroir qui contient la majorité de l’électronique du projet et sur

le côté droit il y a un petit compartiment qui permet de fixer les pompes. Les pièces en bois fixées

à l’aide de colle à bois et ont des enclavures pour augmenter la rigidité et faciliter l’assemblage.

Voici trois vues éclatées de l’assemblage, ainsi qu’une vue d’ensemble.

### 6.1 STATION DE REMPLISSAGE

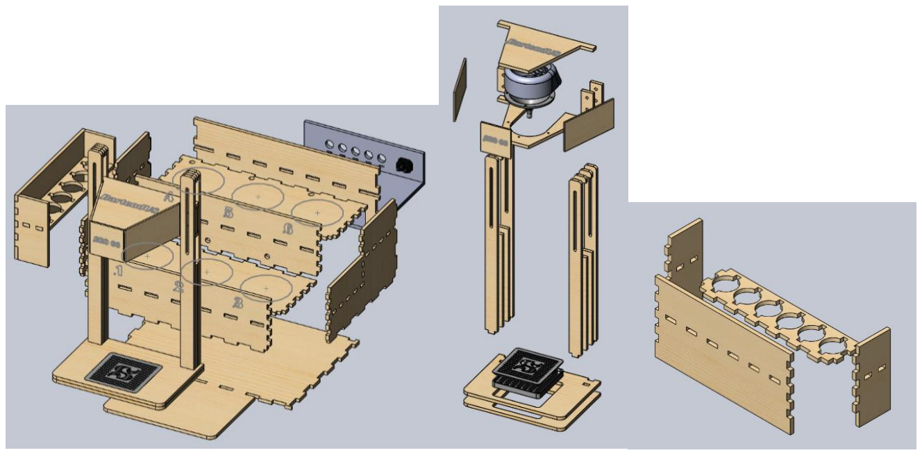
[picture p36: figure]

Figure 1 : Vues éclatées de l'assemblage

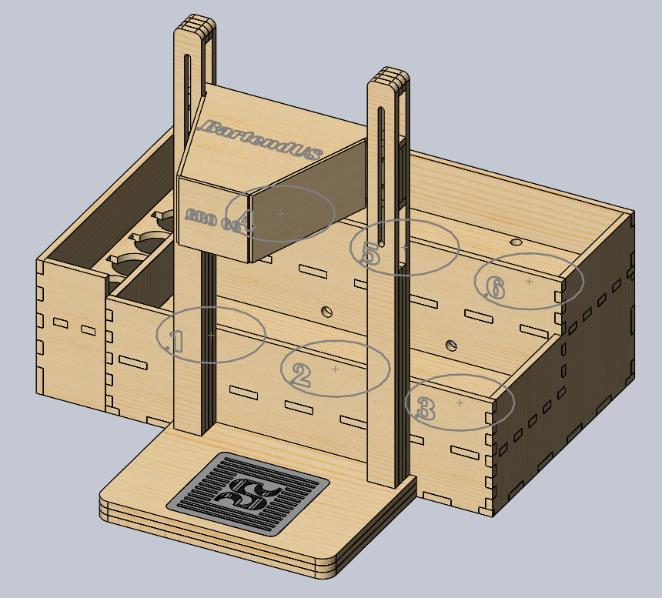
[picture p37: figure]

Figure 2 : Vue d'ensemble

Tout d’abord, il est suggéré de commencer par l’assemblage de la partie station de remplissage.

Il y a quatre pièces à faire imprimer, soit les pièces Receptacle_dessous, Receptacle_dessus,

Entonnoir et upperEntonnoir. Les pièces Recouvrement_poutre_1 et Recouvrement_poutre_2

sont en contreplaqué 1/8 po. Quatre M5 de 35 mm et boulons M5 sont aussi nécessaires.

Une fois les pièces découpées et imprimées il est possible de passer à l’assemblage. Débutez par

coller les pièces Plateforme_dessous et Plateforme_dessus avec la colle à bois et utiliser les serres

pour les maintenir en place. Assurez-vous que les pièces soient alignées en tout temps. Lassez la

colle sécher pendant 1h.

Prenez maintenant les pièces Montant_1, Montant_2 et Montant_3 qui servent à fabrication des

montants. Vous avez besoin de deux exemplaires de chaque pièce pour faire une poutre. Encore

une fois, collez les pièces ensemble avec la colle à bois et utilisez les serres pour sécuriser le tout.

Répétez ces étapes avec la deuxième poutre et laissez sécher pour 1h.

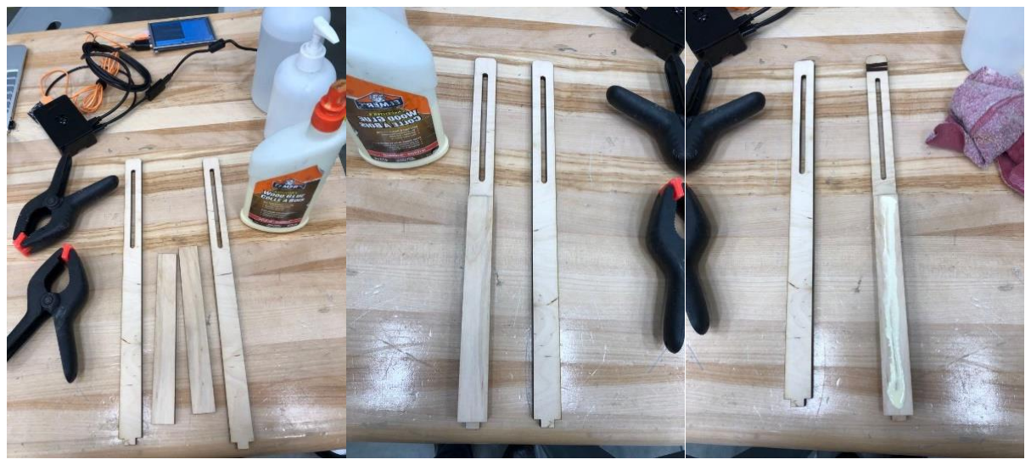
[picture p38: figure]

Ensuite, il est temps de construire la poutre du milieu. Pour ce faire, il vous faut les pièces

Poutre_1, Poutre_2, Poutre_3, Entonnoir et upperEntonnoir ainsi que trois écrous M3 et trois

inserts. Commencez par insérer les inserts dans upperEntonnoir, puis collez cette dernière à

Entonnoir avec le la colle contact.

Utilisez quatre exemplaires de Poutre_3 et collez-les en paires avant de fabriquer le restant de la

poutre. Et laissez sécher pendant 1h.

Collez les deux assemblages des pièces Poutre_3 avec Poutre_1 et Poutre_2. Utiliser un objet

d’environ 2 po d’épaisseur pour soutenir Poutre_2 à son extrémité durant le collage. Laissez

sécher.

Par la suite, utilisez les pièces Recouvrement_poutre_1 et Recouvrement_poutre_2, et collez celle-

ci au-devant et sur les côtés de la poutre. Laisser sécher 1h.

Afin de compléter la poutre, il faut installer l’entonnoir au-dessous avec trois écrous M3.

L’entonnoir doit être placé comme sur l’image suivante.

Prenez maintenant les quatre sous-assemblages faits afin de conclure le montage de la station de

remplissage. Appliquez de la colle aux encastrements dans la base, puis insérez les montants. À

cette étape vous pouvez placer les deux réceptacles dans la base.

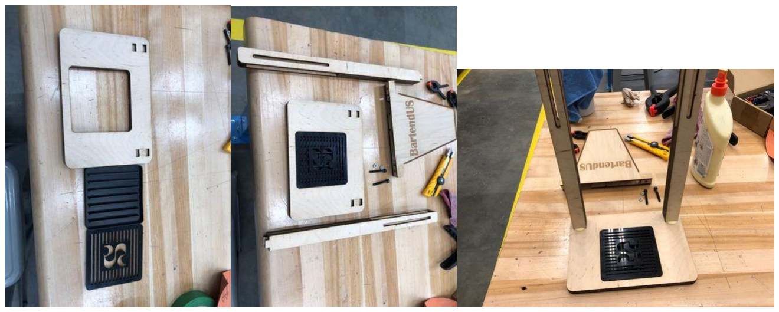
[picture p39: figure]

Ensuite, assemblez la poutre entre les deux montants. Ceci permet de s’assurer que les deux

montants sont droits e parallèles. Laissez le montage sécher pendant 1h et voilà la station de

remplissage complétée!

### 6.2 SUPPORT À POMPES

Ce montage nécessite la fabrication des pièces Supp_pompes_1, Supp_pompes_2,

Supp_pompes_3 et Supp_pompes_4.

Débuter par coller les pièces Supp_pompes_1 et Supp_pompes_2 ainsi.

Continuez l’assemblage en collant les deux exemplaires des pièces Supp_pompe_3 comme ceci.

Terminez cet assemblage en sécurisant les pièces collées à l’aide de serres.

### 6.3 PRÉSENTOIR À BOUTEILLES

Plusieurs pièces sont nécessaires afin de fabriquer le présentoir à bouteilles. Les voici :

- Supp_bout_arriere
- Supp_bout_cote
- Supp_bout_dessous
- Supp_bout_dessus_2
- Supp_bout_dessus_3
- Supp_bout_dev_2
- Supp_bout_dev_3
- porte_arr
- porte_plancher

Le présentoir comporte un tiroir à l’arrière qui sert à ranger l’électronique. Il est préférable de

commencer par l’assemblage de cette partie. Il s’agit simplement de coller les pièces porte_arr et

porte_plancher ensemble ainsi.

Lorsque le tiroir terminé, laissez-le de côté pour sécher. Ensuite, prenez les pièces

Supp_bout_dev_2 et Supp_bout_dessus_2 et fixez-les avec la colle.

Faites de même avec les pièces Supp_bout_dev_3 et Supp_bout_dessus_3.

Appliquez de la colle sur les encoches sur un des côtés de l’assemblage fait jusqu’à présent, puis

insérez-le délicatement dans la pièce Supp_bout_cote.

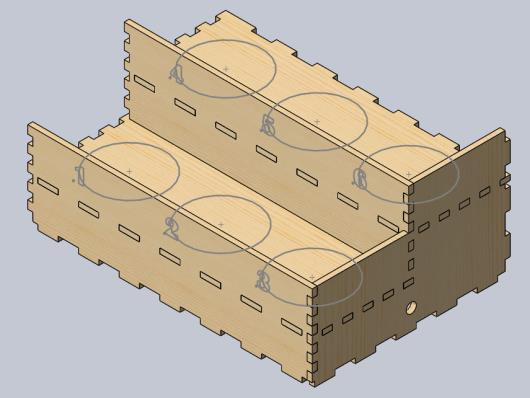
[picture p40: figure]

Répétez la dernière étape avec le deuxième exemplaire de la pièce Supp_bout_cote.

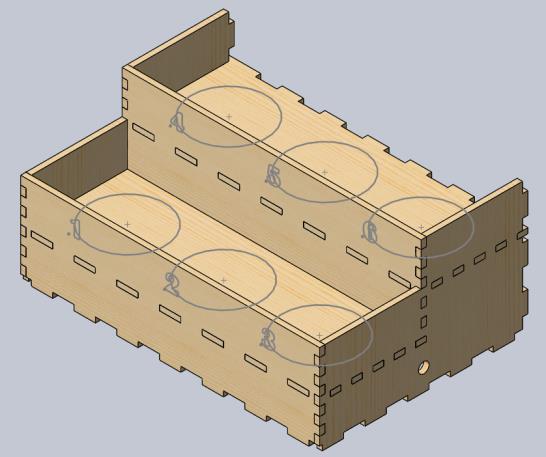
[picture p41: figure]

Puis, fixez l’assemblage complet fabriqué jusqu’à présent sur la pièce Supp_bout_dessous.

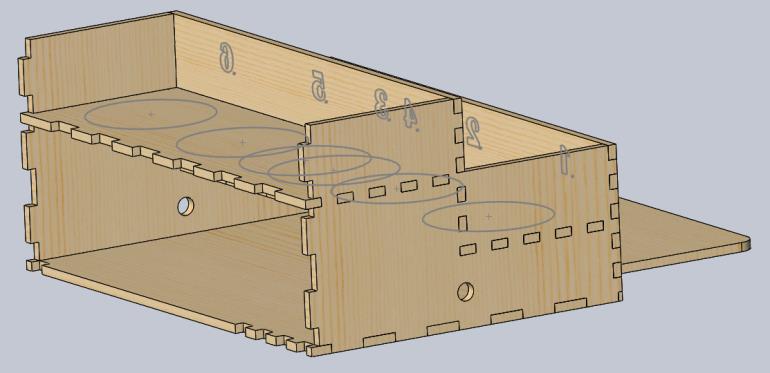
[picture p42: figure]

À l’arrière du présentoir, placez la pièce Supp_bout_arriere.

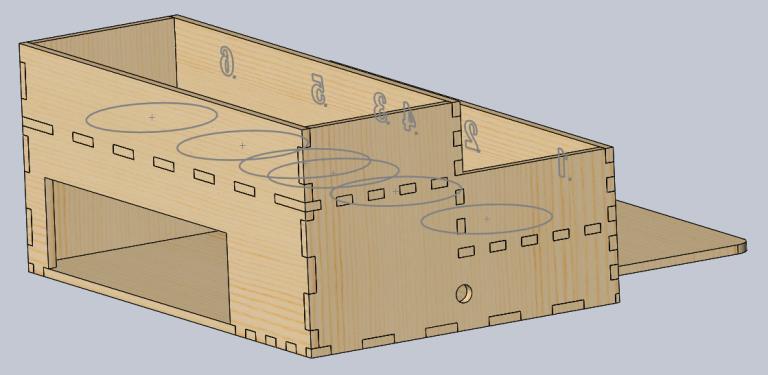
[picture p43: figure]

Utilisez maintenant des serres afin de sécuriser le présentoir et laissez-le sécher. Lorsque le

présentoir est bien sec, collez la station de remplissage à l’avant et le support à pompes sur le

côté désiré du montage. Une fois sec, insérez le tiroir à l’arrière.

Voilà, le montage mécanique de la distribution de liquide est complété.

## 7.SUPPORT DE LA CAMÉRA

Pour ce qui est de la caméra, l’assemblage nécessite des tuyaux d’aluminium. Il faut 1 tuyau de

59 cm et un autre de 32 cm. Pour les fixer ensemble, il suffit d’utiliser la pièce faisant office de

joint au 90° imprimée en 3D.

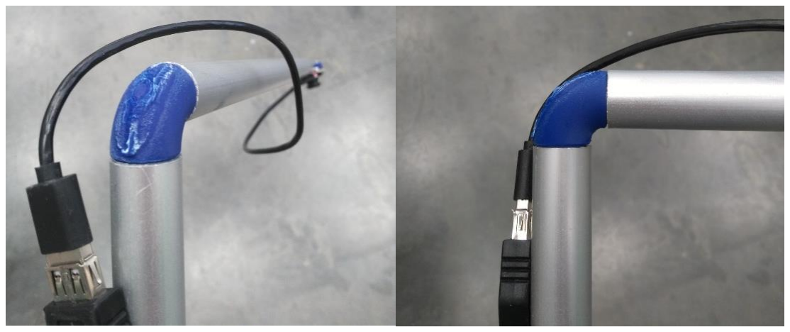
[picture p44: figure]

Installer la caméra au bout avec la pièce prévue à cet effet :

Fixer le fils sur le tube avec un ruban ou le passer à l’intérieur si vous vous faites un câble USB

plus petit pouvant entrer à l’intérieur du tube (« câble custom »).

## 8.SUPPORT À ÉCRAN

Ce petit support à pour but de présenter l’écran à l’utilisateur de manière ergonomique et

esthétique. Il comporte aussi un espace pour ranger le Raspberry Pi 4. Cet assemblage est

complètement fabriqué à l’aide de contreplaqué 1/8 po découpé au laser. Les pièces nécessaires

sont :

- arriere_support_ecran
- face_support_ecran
- montant_exterieur_support_ecran
- montant_exterieur_support_ecran_1_8

- plancher_support_ecran

Commencez le montage en collant les pièces montant_exterieur_support_ecran et

montant_exterieur_support_ecran_1_8 ensemble. Il y une paire de chaque pièce pour faire les

deux montants. Laissez sécher pendant un certain temps.

Par la suite, prenez les pièces plancher_support_ecran et face_support_ecran pour les fixer entre

elles. Laissez sécher pendant un certain temps.

Utilisez maintenant les trois assemblages faits dans les dernières étapes et collez-les. Laisser

sécher ensuite.

La pièce restante, arriere_support_ecran n’est pas collée comme les autres pièces, mais fixée avec

une penture. Voici le résultat final.

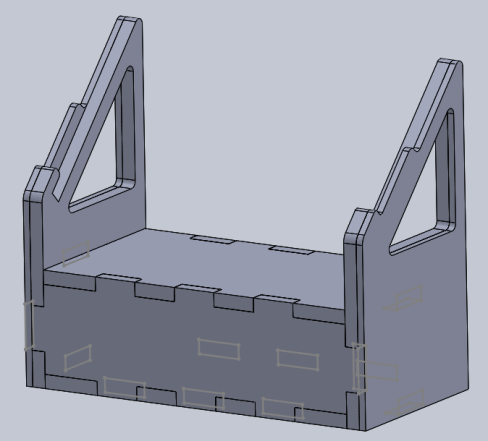
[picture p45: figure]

## 9.ASSEMBLAGE PLATEFORME

La plateforme consiste simplement en une pièce de contreplaqué ¼ po fixée devant le robot.

Celle-ci a une longueur de 75 cm et une largeur de 37,5 cm. Voici où elle doit être placée devant

le robot.

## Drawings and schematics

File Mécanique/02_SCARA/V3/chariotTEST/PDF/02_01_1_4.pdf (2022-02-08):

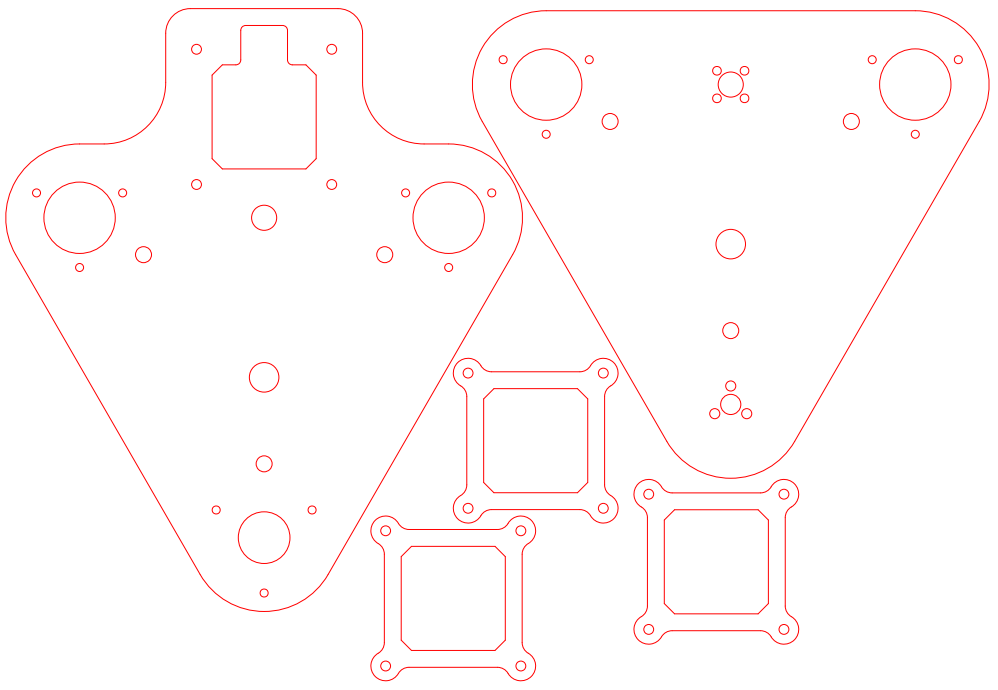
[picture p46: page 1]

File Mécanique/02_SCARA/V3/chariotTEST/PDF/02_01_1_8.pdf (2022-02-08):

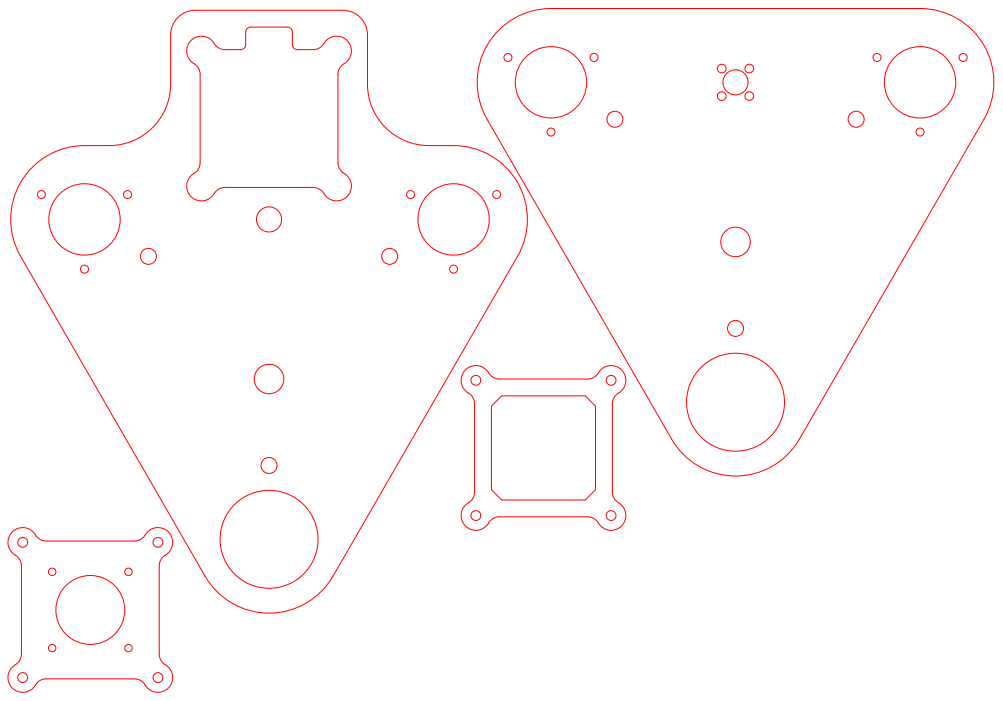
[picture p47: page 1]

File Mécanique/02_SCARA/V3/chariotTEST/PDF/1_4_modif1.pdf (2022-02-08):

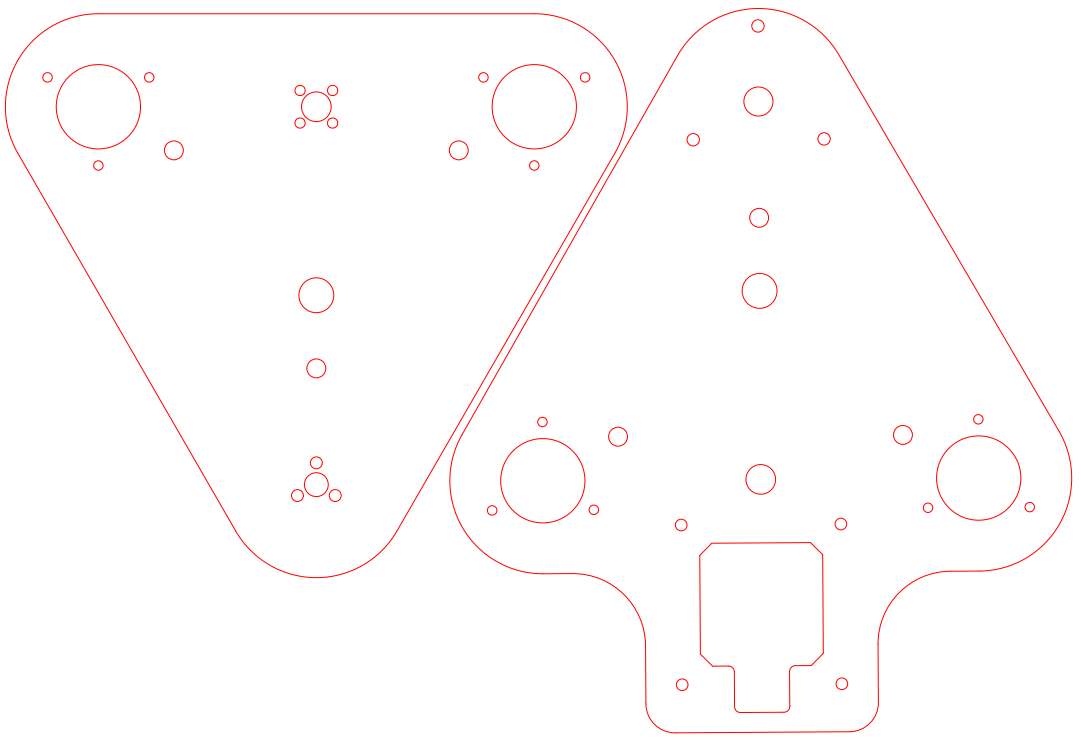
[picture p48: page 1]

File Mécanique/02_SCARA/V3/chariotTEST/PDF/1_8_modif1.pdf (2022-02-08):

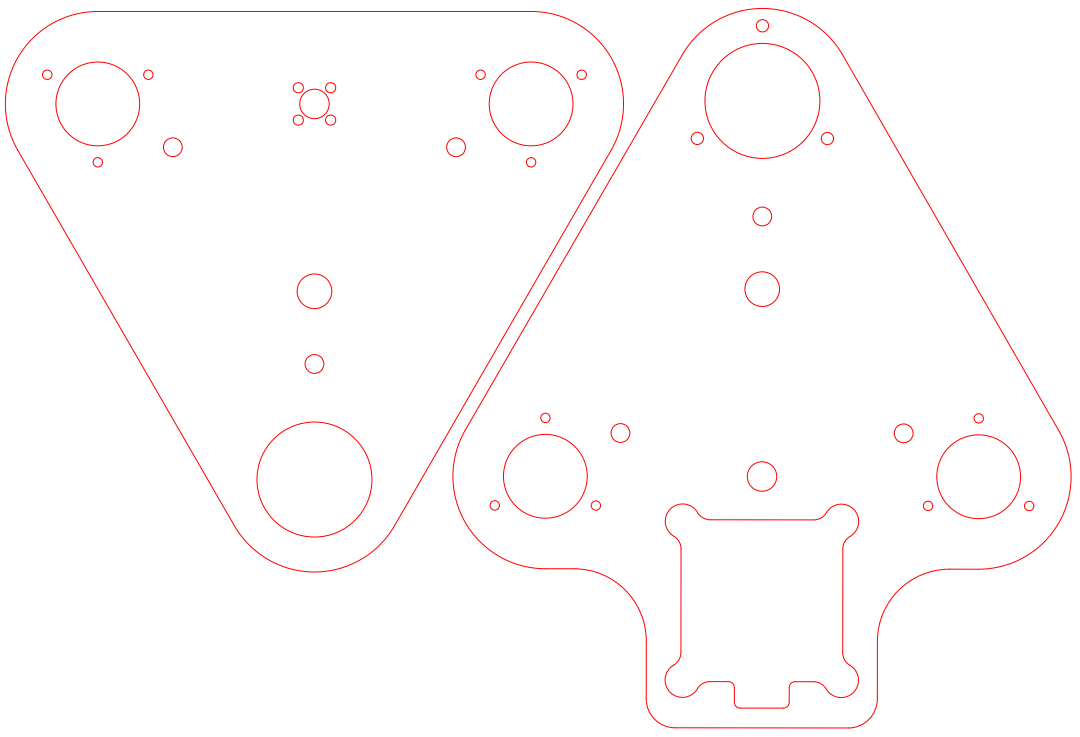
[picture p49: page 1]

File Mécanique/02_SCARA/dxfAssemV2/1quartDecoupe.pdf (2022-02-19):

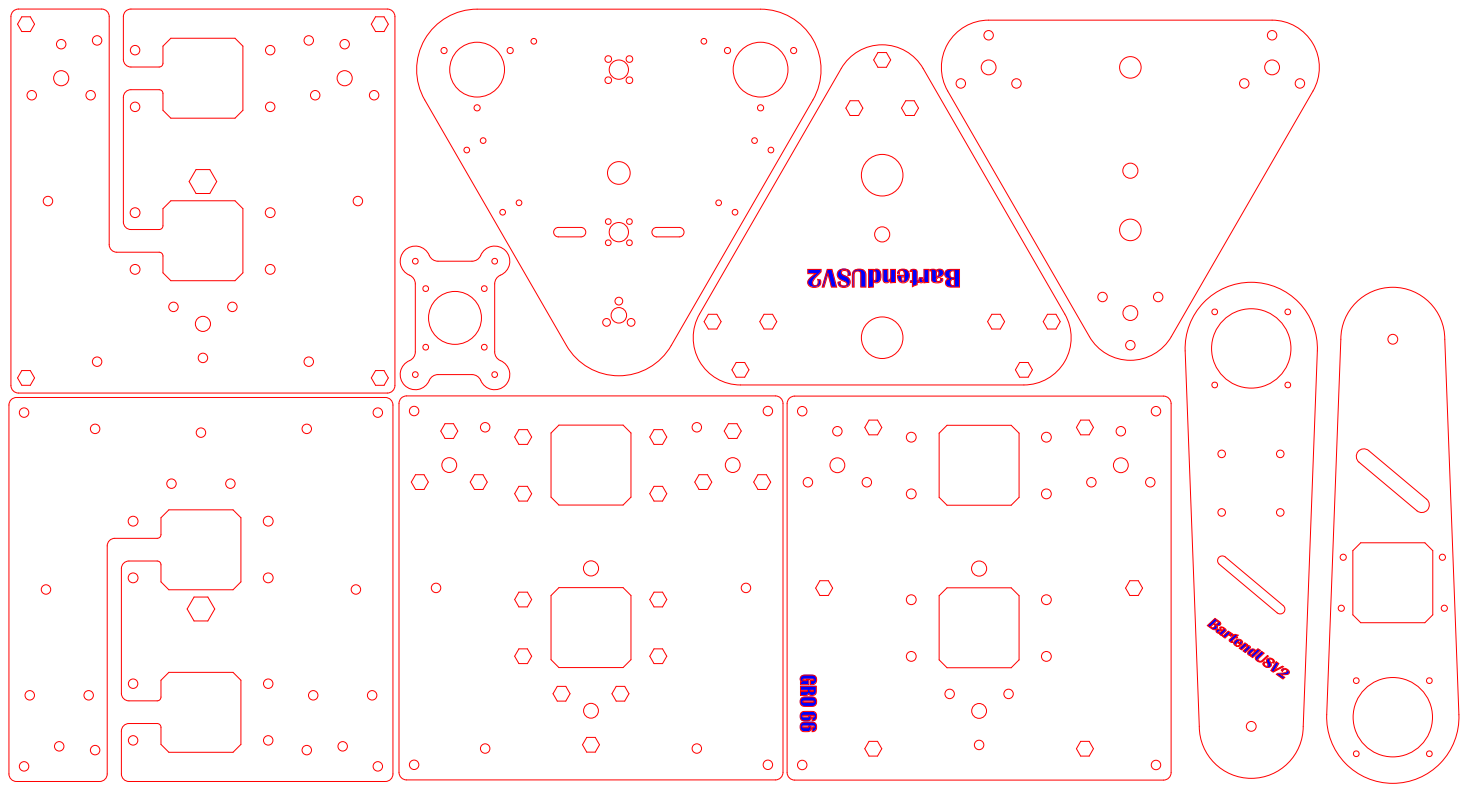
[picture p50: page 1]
BartendUSV

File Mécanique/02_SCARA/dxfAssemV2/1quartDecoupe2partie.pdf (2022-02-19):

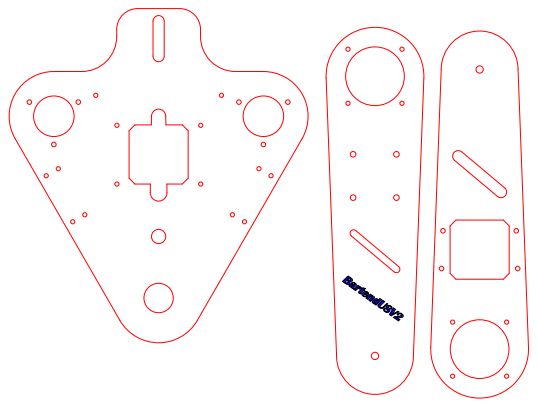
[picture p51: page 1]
BartendUSV2

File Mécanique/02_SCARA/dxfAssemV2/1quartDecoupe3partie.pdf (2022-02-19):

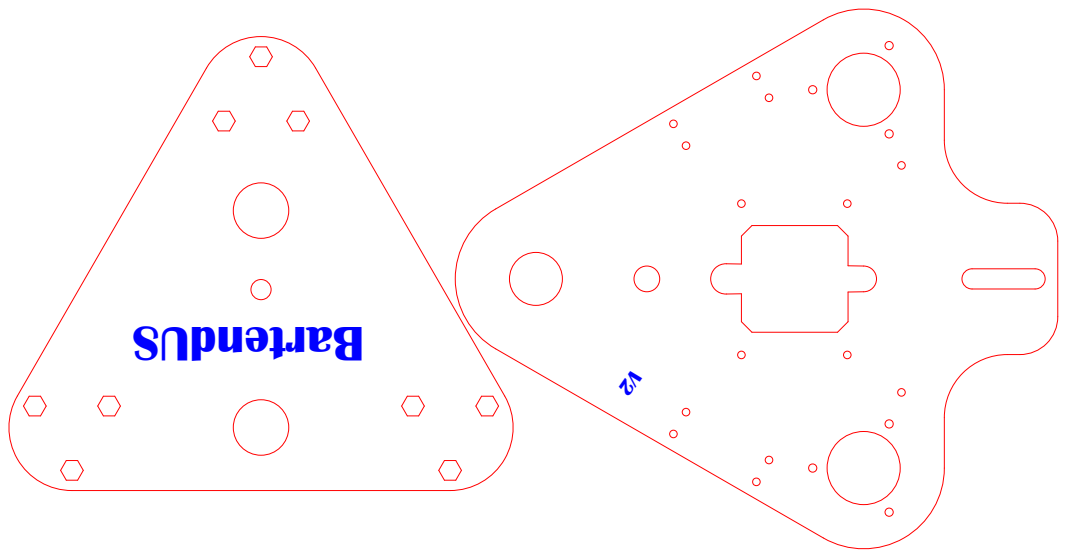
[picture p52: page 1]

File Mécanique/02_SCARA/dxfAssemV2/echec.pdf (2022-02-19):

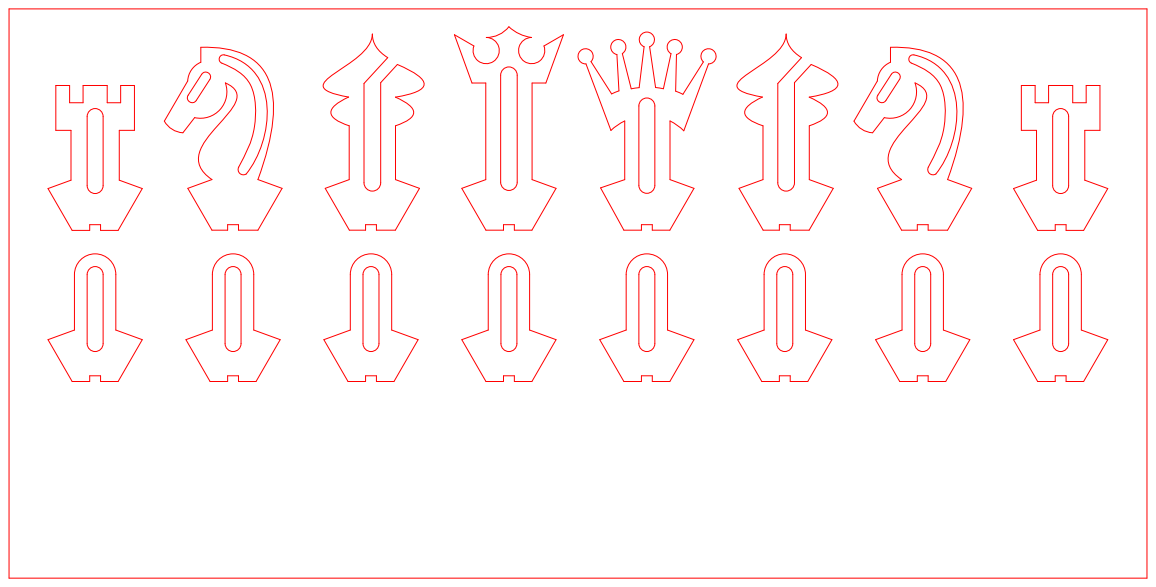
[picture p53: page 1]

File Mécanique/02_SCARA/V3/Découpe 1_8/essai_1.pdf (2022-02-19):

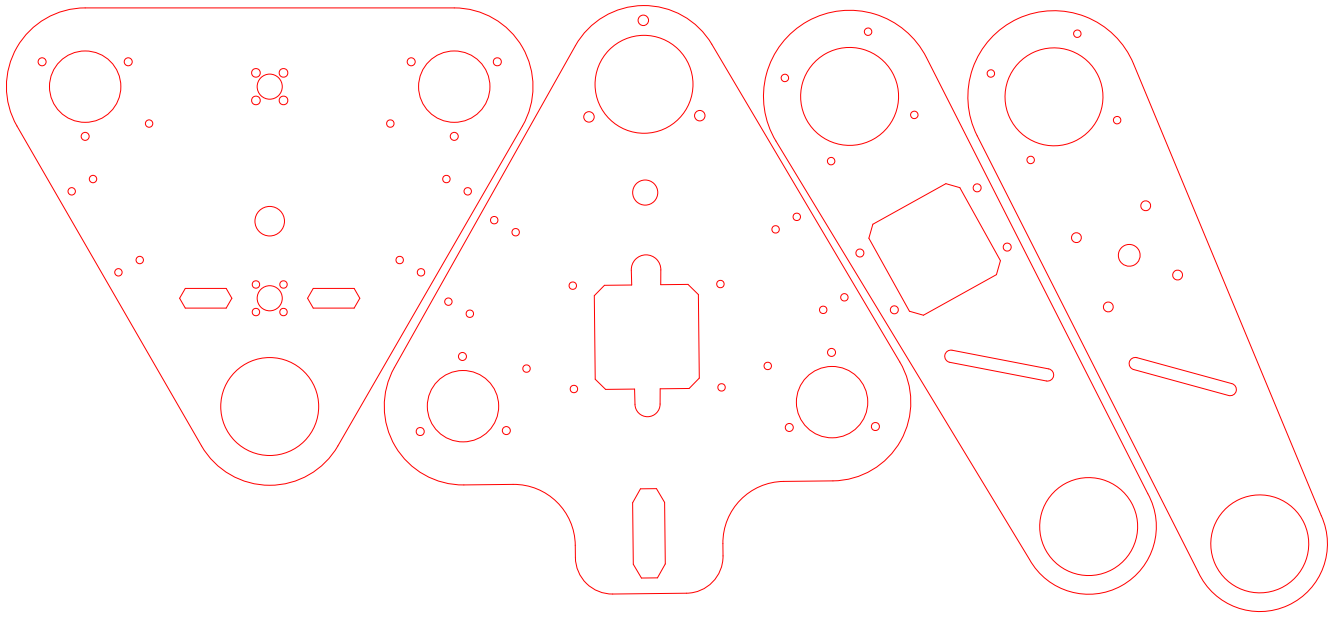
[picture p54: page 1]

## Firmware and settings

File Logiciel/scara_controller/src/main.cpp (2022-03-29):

#include <Arduino.h>
#include <cncShield.h>
#include <string.h>

cncShield* shield;

int state = 0;
int angle = 0;
float angleMotor[3] = {0,0,0};
float lastAngle[3] = {0,0,0};
void setupSerial(void);
void readSerial(void);
void answerSerial(void);

void setup() {
  // Serial.println("Code start here");
  setupSerial();
  shield = new cncShield;
  shield->disableMotor();
}

void loop() {
  readSerial();
  shield->update();
  // shield->motorX->update();
  // shield->motorY->update();
  // shield->motorZ->update();
  // else
  // {
  //   shield->motorX->moveTo(-300);
  // }
  // if(shield->motorY->isMoving())
  // {
  //   shield->motorY->update();
  // }
  // else
  // {
  //   shield->motorY->moveTo(200);
  // }
}

void setupSerial()
{
  Serial.begin(9600);
  Serial.setTimeout(100);
  Serial.flush();
}

void readSerial()
{
  String operatorString = " ";
  int aIndex,bIndex,zIndex;
  String aValue ="",bValue="",zValue="";
  String serialString = "";
  if(Serial.available())
  {
    String tempString = Serial.readStringUntil('\r\n');
    if(tempString[0] != 'G' || tempString[0] != 'M')
      Serial.flush();
    int indexOperator = tempString.indexOf(':');
    operatorString = tempString.substring(0,indexOperator);
    // Serial.print(tempString);
    // Serial.print("  ");
    if(operatorString[0] == 'G') 
    {
      aIndex = tempString.indexOf(':A');
      bIndex = tempString.indexOf(':B',indexOperator+1);
      zIndex = tempString.indexOf(':Z',bIndex+1);
      if(aIndex != -1)
        aValue = tempString.substring(aIndex+1,bIndex-1);
      if(bIndex != -1)
        bValue = tempString.substring(bIndex+1,zIndex-1);
      if(zIndex != -1)
        zValue = tempString.substring(zIndex+1);
      int gNumber = operatorString.substring(1).toInt();

      if(gNumber > 100) // Control pompe
      {
        int pompeNumber = gNumber - 100;
        shield->controlPompe(pompeNumber,aValue.toFloat());
      }
      switch(gNumber)
      {
        case 0: //G0 Move to
          shield->motorA->moveTo(aValue.toFloat());
          shield->motorB->moveTo(bValue.toFloat());
          shield->setNewMouvement();
          // shield->motorZ->moveTo(zValue.toFloat());
          serialString = "Angle set to : A=" + aValue + " B=" + bValue; // + " Z=" + zValue;
          // Serial.println(serialString);
          break;

        case 1: //G1 Set Speed
          // int speedA = aValue.toInt();
          if(aValue.toInt() <= 100 || aValue.toInt() >= 0)
            shield->motorA->setMaxSpeed(aValue.toInt());
          else
            shield->motorA->setMaxSpeed(75);
          // int speedB = bValue.toInt();
          if(bValue.toInt() <= 100 || bValue.toInt() >= 0)
            shield->motorB->setMaxSpeed(bValue.toInt());
          else
            shield->motorB->setMaxSpeed(75);
          // int speedZ = zValue.toInt();
          if(zValue.toInt() <= 100 || zValue.toInt() >= 0)
          {
            shield->motorZ->setMaxSpeed(zValue.toInt());
            shield->motorZ->setSpeed(zValue.toInt());
          }
            
          else
            shield->motorZ->setMaxSpeed(75);
          serialString = "Speed set to : A=" + aValue + " B=" + bValue + " Z=" + zValue;
          // Serial.println(serialString);
          break;

        case 2: //G2 Home
          shield->startHoming();
          // Serial.println("Done");
          break;

        case 3: //G3 Control Z
            shield->motorZ->moveTo(zValue.toFloat());
            shield->setNewMouvement();
            // Serial.println(zValue.toFloat());
            // G3:Z40
          break;

        case 4: //G4 Control poignet
          shield->motorP->setSpeed(8);
          shield->motorP->moveTo(aValue.toFloat());
          shield->setNewMouvement();
          // G4:A40
          break;
          
        case 5: //G5 Control Servo
          if(aValue.toInt() <= 180 || aValue.toInt() >= 0)
          {
            shield->moveServo(aValue.toInt());
            Serial.println("Done");
            // Serial.println("servo Write" + String(aValue));
          }
          break;
        case 6:
          shield->controlPompe(1,aValue.toFloat());
          break;
        
      }
    }
    else if(operatorString[0] == 'M')
    {
      switch(operatorString.substring(1).toInt())
      {
        case 0: // M0 open electro
          // Serial.println("Move servo 0");
          // shield->moveServo(0);
          shield->openElectro();
          answerSerial();
          break;
        case 1: // M1 close electro
        // Serial.println("Move servo 150");
          shield->closeElectro();
          answerSerial();
          // code
          break;
        case 3: 
          shield->startShake();
          break;
        case 4:
          shield->startVerser(1);
          break;
        case 5:
          shield->startVerser(-1);
          break;
        case 10:
          shield->disableMotor();
          break;
        case 11:
          shield->enableMotor();
          break;
      }
    }
  }
  
}

void answerSerial()
{
  Serial.println("Done");
}

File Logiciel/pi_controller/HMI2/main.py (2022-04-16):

import sys
import time
#from calibration import Calibration_cam
#from Vision.calibration import Calibration_cam
from PyQt5.uic import loadUi
from PyQt5 import QtWidgets as qtw
from PyQt5.QtWidgets import QDialog, QApplication, QInputDialog, QListWidgetItem, QPushButton, QMessageBox
from PyQt5.QtCore import QObject, QThread, pyqtSignal
from PyQt5.uic.properties import QtGui

from Logiciel.pi_controller.HMI2.librairieRecette import gestion_Recette,gestion_ingredient_dispo,recette
from Logiciel.pi_controller.HMI2.stateMachine import sequence
from Vision.calibration import Calibration_cam
import serial.tools.list_ports
from PyQt5.QtWidgets import QDialog, QApplication, QGraphicsScene, QGraphicsPixmapItem
from PyQt5.QtGui import QPixmap


#init des variables globales
livreRecette=gestion_Recette()
livreIngredient=gestion_ingredient_dispo()
#calib = Calibration_cam()
max_Bouteille=6
sequence=sequence()


# Step 1: Create a worker class
class Worker(QObject):
    finished = pyqtSignal()
    progress = pyqtSignal(object)
    enCours = pyqtSignal(bool)
    erreur = pyqtSignal(object)
    success = pyqtSignal()

    def ajouterRecette(self,recette):
        self.recette = recette

    def run(self):
        #TODO gestion erreur calibration camera, position impossible a atteindre ou aucun verre

        mess_seq=sequence.sequence(self.recette,livreIngredient)
        if(mess_seq !=""):
            self.erreur.emit(mess_seq)
        else:
            #self.recalibration()
            self.success.emit()

        self.finished.emit()


class MainWindow(QDialog):
    def __init__(self):
        print("refresh")
        super(MainWindow, self).__init__()
        loadUi("pi_controller/HMI2/MainWindow_test.ui", self)
        self.recettes.clicked.connect(self.go_to_recettes)
        self.boire.clicked.connect(self.go_to_boire)
        self.bouteilles.clicked.connect(self.go_to_bouteilles)
        self.reglages.clicked.connect(self.go_to_reglages)

    def go_to_recettes(self):
        screen5 = consulter_recettes_screen5()
        widget.addWidget(screen5)
        widget.setCurrentIndex(widget.currentIndex()+1)

    def go_to_boire(self):
        screen3 = boire_screen3()
        widget.addWidget(screen3)
        widget.setCurrentIndex(widget.currentIndex()+1)
        screen3.recettes_disponibles.setCurrentRow(-1)

    def go_to_bouteilles(self):
        screen4 = bouteilles_screen4()
        widget.addWidget(screen4)
        widget.setCurrentIndex(widget.currentIndex() + 1)

    def go_to_reglages(self):
        screen5 = reglages_screen5()
        widget.addWidget(screen5)
        widget.setCurrentIndex(widget.currentIndex() + 1)





#*****************************************************************************************************WINDOW RECETTE
class recette_screen2(QDialog):
    def __init__(self):
        super(recette_screen2, self).__init__()
        loadUi("pi_controller/HMI2/recette.ui", self)

        self.precedent.clicked.connect(self.go_to_recettes)
        self.ajouter_alcool.clicked.connect(self.ajouter_ingredient)
        self.ajouter_recette.clicked.connect(self.ajouter_livreRecette)
        self.supprimer.clicked.connect(self.supprimer_ligne)
        #self.delete_all.clicked.connect(self.supprimer_tout)
        self.liste_ingredient_recette=[]
        self.liste_quantite_recette=[]

    def go_to_recettes(self):
        screen5 = consulter_recettes_screen5()
        widget.addWidget(screen5)
        widget.setCurrentIndex(widget.currentIndex()+1)

    def ajouter_ingredient(self):

        alcool = self.alcool_ligne.text()
        quantite = self.quantite_ligne.text()

        if (alcool.find(":") != -1 or alcool.find(",") != -1 or alcool.find("/") != -1):
            qtw.QMessageBox.information(self, 'Erreur caractère',
                                        '''Les caractère : ":" "," "/" ne sont pas acceptés''')
            return
        else:
            pass
        if alcool == "":
            qtw.QMessageBox.information(self, 'Attention', '''Aucun alcool entrée'''+ "\n" + '''Réessayer...''')
            return
        try:
            quantite=float(quantite)
        except:
            qtw.QMessageBox.information(self, 'Erreur',
                                        '''La quantité "''' + quantite + '''" n'est pas un chiffre.''' + "\n" + '''Réessayer...''')
            return

        if quantite > 8:
            qtw.QMessageBox.information(self, 'Attention', '''La quantité d'alcool est supérieure à 8 oz'''+ "\n" + '''Réessayer...''')
            return

        self.liste_ingredient_recette.append(alcool)
        self.liste_quantite_recette.append(quantite)

        chaine_temp = alcool + ': ' + str(quantite) + 'oz'
        self.listWidget.addItem(chaine_temp)

        self.alcool_ligne.setText('')
        self.alcool_ligne.setFocus()
        self.quantite_ligne.setText('')
        self.quantite_ligne.setFocus()

    def supprimer_ligne(self):
        row=self.listWidget.currentRow()
        if(row>=0):
            self.listWidget.takeItem(row)
            self.liste_ingredient_recette.pop(row)
            self.liste_quantite_recette.pop(row)


    # def supprimer_tout(self):
    #     self.listWidget.clear()
    #     self.liste_ingredient_recette.clear()
    #     self.liste_quantite_recette.clear()

    def ajouter_livreRecette(self):

        titre = self.titre_ligne.text()
        if titre == "":
            qtw.QMessageBox.information(self, 'Erreur entrée','''Aucun titre''' + "\n" + '''Réessayer...''')
            return

        if len(self.liste_ingredient_recette)<1:
            qtw.QMessageBox.information(self, 'Erreur entrée', '''Aucun ingrédient''' + "\n" + '''Ajoutez au moins un ingrédient...''')
            return

        livreRecette.ajouterRecette(titre,self.liste_ingredient_recette,self.liste_quantite_recette)
        livreRecette.update_recette_dispo(livreIngredient)
        self.liste_ingredient_recette.clear()
        self.liste_quantite_recette.clear()
        self.listWidget.clear()
        #clear le texte des boites
        self.alcool_ligne.setText('')
        self.alcool_ligne.setFocus()
        self.titre_ligne.setText('')
        self.titre_ligne.setFocus()
        self.quantite_ligne.setText('')
        self.quantite_ligne.setFocus()
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

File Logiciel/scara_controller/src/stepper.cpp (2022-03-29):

#include <stepper.h>

Stepper::Stepper(){
};

Stepper::Stepper(int dirPin, int stepPin,int microstep, float gearRatio)
{
    _gearRatio = gearRatio;
    _microstep = microstep;
    this->setpin(dirPin,stepPin);
    this->setDirection(1);
    digitalWrite(_dirPin,LOW);
    digitalWrite(_stepPin,LOW);
    _maxSpeed = 100;
    _currentPosition = 0;
    _stepCount = 0;
    _stepAccel = 0;
    _timeAcc = 2;
    _setupAcc = 1;
};

bool Stepper::update(bool accel)
{
    if(_stepCount != 0)
    {
        if(accel)
            updateAccelV2();
        if(micros() - _lastTime >= _delaySpeed)
        {
            if(_flipflopStep&0x01)
            {
                digitalWrite(_stepPin,HIGH);
            }
            else
            {
                digitalWrite(_stepPin,LOW);
                _stepCount --;
            }
            _flipflopStep++;
            _lastTime = micros();
        }
        
        // _currentPosition = _stepCount;
        return 1;
    }
    else
    {
        return 0;
    }
};

void Stepper::updateAccel()
{
    int tempSpeed = 0;
    if(_stepCount <= (_calculStepAccel *6) && _stepCount > (_calculStepAccel *4))
    {
        tempSpeed = map(_stepCount,(_calculStepAccel*6),(_calculStepAccel*4),(_maxSpeed*0.25),_maxSpeed);
        this->setSpeed(int(tempSpeed));
    }
    else if(_stepCount <= (_calculStepAccel *4) && _stepCount > (_calculStepAccel *2))
    {
        this->setSpeed(int(_speed));
    }
    else if(_stepCount <= (_calculStepAccel *2) && _stepCount > (_calculStepAccel *0))
    {
        tempSpeed = map(_stepCount,(_calculStepAccel*0),(_calculStepAccel*2),(_maxSpeed*0.25),_maxSpeed);
        this->setSpeed(int(tempSpeed));
    }
}

void Stepper::updateAccelV2()
{
    if(millis() - _lastTimeAcc >= _timeAcc)
    {
        _lastTimeAcc = millis();
        if(_setupAcc)
        {
            _setupAcc = 0;
            this->setSpeed(int(_maxSpeed*0.25));
        }
        if(_stepCount >= _calculStepAccel*2)
        {
            if(_speed < _maxSpeed)
            {
                this->setSpeed(_speed + 0.2);
            }
            // premiere moitier du parcour

        }
        else if(_stepCount < _calculStepAccel*2)
        {
            // deuxieme moititier du parcour
            // if(_speed > abs(_maxSpeed/2))
            // {
            //     this->setSpeed(_speed - 5);
            // }
            if(_speed > (_maxSpeed*0.25))
            {
                this->setSpeed((_speed - 0.5));
            }

            if(_stepCount == 1)
            {
                _setupAcc = 1;
            }
        }
    }
    
}

bool Stepper::moveTo(float degree)
{
    if(_stepCount != 0)
        return EXIT_FAILURE;
    if(_direction == 1 || _direction == -1)
        degree = degree * _direction;
    float deltaPos = _currentPosition - degree;
    if(degree > _currentPosition)
        digitalWrite(_dirPin,LOW);
    else
        digitalWrite(_dirPin,HIGH);
    
        
    // Serial.println(degree);
    if(degree == _currentPosition)
        return EXIT_FAILURE;
    
    _currentPosition = degree;
    _stepCount = int((abs(deltaPos) * _gearRatio * _microstep * 200.0) /360); 
    _calculStepAccel = _stepCount / 6;
    _lastTime = micros();
    _lastTimeAcc = millis();
    // Serial.println("step count : " + String(_stepCount));
    
    return EXIT_SUCCESS;
};

bool Stepper::isMoving()
{
    if(_stepCount != 0)
        return 1;
    else
        return 0;
};

void Stepper::setpin(int dirPin, int stepPin)
{
    _dirPin = dirPin;
    _stepPin = stepPin;

    pinMode(_dirPin,OUTPUT);
    pinMode(_stepPin,OUTPUT);
};

void Stepper::setGearRatio(float gearRatio)
{
    _gearRatio = gearRatio;
};

float Stepper::getCurrentPosition()
{
    return _currentPosition;
};

void Stepper::setCurrentPosition(float position)
{
    _currentPosition = position;
    _stepCount = 0;

}

void Stepper::setMaxSpeed(int speed)
{
    _maxSpeed = speed;
};

void Stepper::setSpeed(float speed)
{
    if(speed > 100.0)
        speed = 100.0;
    if(speed < 0.0)
        speed = 0.0;
    _speed = speed;
    int tempSpeed = _speed * 10;
    _delaySpeed = map(tempSpeed,0,1000,1000,80);
    // Serial.println(_delaySpeed);
};

void Stepper::setMicroStep(int microstep)
{
    _microstep = microstep;
};

void Stepper::setDirection(int direction)
{
    if(direction == 1 || direction == -1)
        _direction = direction;
};

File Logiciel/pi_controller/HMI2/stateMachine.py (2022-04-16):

import subprocess
import sys
import glob
import cv2
import serial
import time
from Logiciel.pi_controller.HMI2.inverseKinematic import scaraRobot
from Vision.calibration import Calibration_cam
from PIL import Image
import subprocess
import numpy as np

class sequence():

    def __init__(self):
        #raspPi : '/dev/ttyUSB0'    #ordi : port=COM3
        #self.arduino = serial.Serial(port='COM3', baudrate=9600, timeout=.1)     # Pour le Pi
        self.r= scaraRobot()
        self.calib = Calibration_cam



    def send_message(self, message,wait):
        try:
            print(message)
            #self.arduino.reset_input_buffer()
            self.arduino.write(bytes(message, 'utf-8'))
            time.sleep(0.05) # one tick delay (15ms) in between reads for stability
            print("data sent")

            if wait :
                done=False
                while(not done):
                    try :
                        dataIn = str(self.arduino.readline())
                        # print(dataIn)
                        if dataIn.find("Done") != -1:
                            done=True
                    except:
                        done=False

                    time.sleep(0.05)
        except:
            print("erreur aucun port sélectionné")
        return

    def openSerial(self, port_com):
        # open the serial port selon lui qui a ete choisi dans le ComboBox du HMI.
        try:
            self.arduino = serial.Serial(port=port_com, baudrate=9600, timeout=.1)
            time.sleep(0.5)
            self.arduino.reset_input_buffer()
            self.send_message("M11\r\n", False)
        except:
            pass
    
    # en deg
    def poignet(self,angle,wait):
        position = "G4:A" + str(angle) + "\r\n"
        self.send_message(position,wait)
        return

    def servo(self,angle,wait):
        position = "G5:A" + str(angle) + "\r\n"
        self.send_message(position,wait)
        return

    def electro(self,activate,wait):
        if activate:
            position = "M1" + "\r\n"
            self.send_message(position,wait)
        else:
            position = "M0" + "\r\n"
            self.send_message(position,wait)
        return

    def moveUpDown(self,z,wait):
        position = "G3:Z" + str(z) + "\r\n"
        self.send_message(position,wait)
        return

    def moveTo(self,x, y,wait):
        self.r.inverseKinematic([x, y])
        angles = self.r.getAngleDeg()
        print(x,y)
        print(angles)
        position = "G0:A" + str(angles[0]) + ":B" + str(angles[1]) + "\r\n"
        print(position)
        self.send_message(position,wait)
        return

    def homing(self,wait):
        # caller la fonction HOME
        homing = "G2\r\n"
        self.send_message(homing,wait)
        self.moveTo(0.49,0,wait)
        self.moveUpDown(15, wait)
        return

    def activatePompe(self,list_pompe, list_quant,wait):
        # G101:A1.5 pour la pompe 1 avec 1.5oz
        print(list_pompe)
        print(list_quant)

        for i in range(len(list_pompe)):
            pompe = "G10" + str(list_pompe[i]) + ":A" + str(list_quant[i]) + "\r\n"
            self.send_message(pompe,wait)
            #livreIngredient.update_Quantite(index,quantite)
        return


    def sequence(self,recette,livreIngredient):
        wait=True
        self.moveUpDown(15,wait)
        self.moveTo(0.49,0,wait)

        if self.calib.calib_vision_seuil is False:
            return "Veuillez recalibrer la caméra dans la fenêtre réglage"
        else:
            positionVerre=self.vision()
            print(positionVerre)

            if(self.r.isInEnvloppe(positionVerre) is False):
                return "Verre inaccessible! Êtes vous trop chôoo?\nPlacez votre verre et recommander"

            if(positionVerre[0]==0 and positionVerre[1]==0):
                return "Aucun verre détecté! Êtes vous trop chôoo?\nPlacez votre verre et recommander"
            else:

                #self.moveTo(0.36,0.10,wait)
                self.servo(180,wait)
                self.moveUpDown(60, wait)
                self.moveTo(0.47, 0.04, wait)
                self.moveTo(0.285,-0.03,wait)
                if (self.pompe(recette,livreIngredient,wait) is False):
                    self.moveTo(0.47, 0.04, wait)
                    self.servo(5, wait)
                    return "Quantité insuffisante d'un ingrédient"
                else:
                    time.sleep(5)
                    #self.moveTo(0.49,0,wait)
                    self.moveTo(0.47,0.04,wait)
                    self.servo(5,wait)
                    self.moveUpDown(210,wait)
                    self.moveTo(0.40, 0.25, wait)
                    self.shake(wait)


                    #positionVerre=[-0.15, 0.4]
                    pos = self.r.tangentAuVerre(positionVerre)
                    self.moveTo(pos[0],pos[1],wait)
                    self.servo(40,wait)

                    sens = self.r.getSensVersement()
                    if(sens=="gauche"):
                        self.poignet(70,wait)
                    else:
                        self.poignet(-70,wait)

                self.versement(sens,wait)
                self.servo(5,wait)
                self.moveTo(0.49, 0, wait)
                return ""

    def versement(self,sens,wait):
        # caller la fonction HOME
        if sens == "gauche":
            versementMessage = "M4\r\n"
        else:
            versementMessage = "M5\r\n"
        self.send_message(versementMessage,wait)
        return
    
    # retourne la position et le temps de chacune des pompes a actionner
    def identification_pompe(self,recette, livreIngredient):
        conv=0.5
        print(recette)
        self.list_position_pompe = []
        self.list_quant_pompe = []

        self.list_ingredient_dispo = livreIngredient.get_list_ingredient().copy()
        self.list_quantite_ingredient_dispo = livreIngredient.get_list_quantite().copy()
        self.list_pos_bouteille = livreIngredient.get_list_position().copy()

        self.list_ingredient = recette.getlistAlcool().copy()
        self.list_quantite = recette.getlistQuantite().copy()

        for i in range(len(self.list_ingredient)):
            for j in range(len(self.list_ingredient_dispo)):
                if self.list_ingredient_dispo[j] == self.list_ingredient[i]:
                    if float(self.list_quantite_ingredient_dispo[j])<float(self.list_quantite[i]):
                        return False
                    else:
                        self.list_position_pompe.append(self.list_pos_bouteille[j])
                        self.list_quant_pompe.append(self.list_quantite[i])
                        # remove from next search
                        #self.list_ingredient_dispo.pop(j)
                        #self.list_pos_bouteille.pop(j)


        return [self.list_position_pompe, self.list_quant_pompe]
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

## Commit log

2022-01-26 CAD update
    [00_Assy_BartendUS.SLDASM, 02_00_Assy_SCARA_V1.SLDASM, 02_012_deuxieme_v2_niveau_base.SLDPRT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]
2022-01-26 stepper driver done. To be tested
2022-02-08 Update CAD + Excel COM Software
    [02_012_deuxieme_v2_niveau_base.DXF, 02_012_deuxieme_v2_niveau_base.SLDPRT, 02_01_Assy_base_z_axis_V1.SLDASM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]
2022-02-11 Serial python working with Arduino, Accel not working anymore
    [Serial_Communication_Code.xlsx]
2022-02-16 cinematique inverse ainsi qu'une simulation des segmnents robots
2022-02-16 Creation de readme.md pour la partie mécanique
2022-02-19 Mise à jour fichiers CAD
    [02_012_deuxieme_v2_niveau_base.SLDPRT, 02_012_deuxieme_v2_niveau_base_1_quart.DXF, 02_01_Assy_base_z_axis_V1.SLDASM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]
2022-02-19 Conversion en français noms classeurs
    [00_Assy_BartendUS.SLDASM, 02_00_Assy_SCARA_V1.SLDASM, 02_012_deuxieme_v2_niveau_base.DXF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]
2022-02-20 Homing for A-B added + non-blocking update for motor
2022-02-21 ajout de certaines fonctions activation des actuateurs linéaires avec radio bouton, Home
2022-02-22 config for homing done, angle + direction are good
2022-02-22 ajout cinematique + homing au main
2022-02-22 First commit for vision calibration
2022-02-23 code fonctionnel , implementation camera dans main
2022-02-23 Updated CAD files
    Mise à jour des fichiers CAD sur le GitHub selon les derniers changements
    [Actuateur_linéaire.SLDPRT, Asm_TEST_supp_distri.SLDASM, Levier_1.DXF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]
2022-03-03 Réorganisation du code calibration.py, toujours en période de test
2022-03-09 Ajout des points provenant de l'image de référence sur l'image projetée en temps réelle sur le HMI dans calibration.py
2022-03-10 Modification de calibration.py en classe Calibration_cam() + ajout méthode pour tenir compte du seuil de comparaison + création méthode popup HMI
2022-03-13 Changements dans le main de calibration.py
2022-03-16 offsetTangent au verre implementation 1, bug
    [inverseKinematic.py]
2022-03-17 update servo + electro
2022-03-17 implementation class ingredient ajout fonction recette correction bug
    [librairieRecette.py]
2022-03-19 implementation fonction communication arduino pour mouvement
2022-03-19 Z added + homing, Poignet added. All Serial command
2022-03-21 implementation BACK-end Hmi, thread, gestion des recettes dans HMI
2022-03-22 correction Bug ecriture recette/ingredient
    [main.py]
2022-03-22 Mise en commun du travail du code de Tony et de Simon (ajout de la classe reglages)
2022-03-22 mise en place des fonctions de communication
2022-03-24 Oublie de push (modif fait durant la journee de projet)
2022-03-24 changement de taille des fenetres (1280 X 720)
2022-03-25 blindage gestion des ingredients
2022-03-25 Gestion des returns dans calibration.py pour utilisation dans la state machine
2022-03-26 Afficher image calib plein écran + tests calib-HMI réussis + modification des paths pour l'image de référence
2022-03-26 Modification de la fonction calcul du seuil plus efficace + test réussi
2022-03-27 detecte sens versement selon la position du verre
2022-03-28 option wait dans send_message pour attendre le feedback arduino, debug thread sequence
2022-03-28 finition de certaines tailles de boutons pour l'ecran de 7 po (proche du resultat final)
2022-03-29 Vision Raspberry Pi
2022-03-29 Tune up calibration
2022-03-30 Ménage de code, indentation et commentaires
2022-03-30 passage d'argument recette au thread et à la sequence
2022-03-30 gestion des erreur lors des commandes d'un verre ( calib+pompe+detection)
2022-03-30 Ajout d'headers de fonctions et cleanup du code calibration.py
2022-03-30 Séquence complète fonctionnelle - Reste à avoir la plateforme finale + tests cam final
2022-04-06 update des path
2022-04-06 gestion des caracteres invalides + gestion quantite de liquide par bouteille
2022-04-06 camera fonctionnal , ajout state machine
2022-04-13 update file pi error
    [cncShield.cpp, cncShield.h, inverseKinematic.py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]
2022-04-13 Commit FINAL FINAL after git issues
    [cncShield.cpp, cncShield.h, inverseKinematic.py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]
2022-04-13 update des liquides bouteilles
2022-04-14 Ajout d'headers de fonctions dans calibration.py
2022-04-14 Update fichiers CAD
    [02_06_troixieme_niveau_base.SLDPRT, 02_08_support_base_vertical.SLDPRT, 02_13_support_rodes_8mm_haut.SLDPRT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]
2022-04-14 Ajout guide d'assemblage robot dans le dossier mécanique
2022-04-16 BOM modifs
2022-04-16 Mise à jour guide d'assemblage du robot
